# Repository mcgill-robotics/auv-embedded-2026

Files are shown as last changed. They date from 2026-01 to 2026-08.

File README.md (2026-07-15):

# McGill Robotics AUV Embedded 2026

Welcome to the AUV Embedded 2026 repository! This repository is created and maintained by the 2026 McGill Robotics AUV Electrical team. It serves as a platform for sharing, calibrating, and version-controlling the embedded software we develop for our Autonomous Underwater Vehicle (AUV).

## About Us

We are a dedicated team of students from McGill Robotics, focused on designing and implementing the PCBs and embedded systems that power our underwater robot. Our mission is to enable autonomous navigation and task performance through advanced electrical engineering and software development.

## What You'll Find Here

- **Embedded Software**: Source code and libraries for our AUV's embedded systems.
- **Team Structure**: Information about our team members and roles.
- **Tutorials**: Guides and tutorials on using ROS (Robot Operating System) and Arduino for our projects.

For more detail please visit our [Wiki](https://github.com/mcgill-robotics/auv-embedded-2026/wiki).

## Hydrophone related work 

You will find in the `dev/hydrophone` branch the following folders : 
- `documentation`, documenting the design of the new hydrophone ADC board. The documentation was written using _mkdocs_, and to view it you'll need to 1. clone the repository locally, then install mkdocs using `pip install mkdocs` and finally render the web documentation using `mkdocs serve` _in the `documentation` folder_
- `kicad`, which contains the source files (`ADC.kicad_pro`) for the design of the new ADC board
- `ltspice`, for the LTSPICE simulations of the ADC board signal chain.

If you have any questions regarding the hydrophone board design please contact @Oscar-T24

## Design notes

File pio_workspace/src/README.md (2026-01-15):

# Source Code Overview

This directory contains the embedded source code for the McGill Robotics AUV systems. The code is responsible for interfacing with onboard hardware, running micro ROS nodes, and publishing sensor data to the ROS 2 network.

---

## Display Board

The Display Board firmware is implemented in `display_main.cpp`. In addition to handling the TFT display and touchscreen, this board interfaces with a pressure sensor and publishes depth data over micro ROS.

---

## ROS 2 Topics

The following ROS 2 topics are published by the Display Board (`display_main.cpp`).

### Depth Sensor Publisher
- **Node:** `display_node`
- **Source File:** `display_main.cpp`
- **Topic:** `/sensors/depth/z`
- **Message Type:** `std_msgs/msg/Float64`
- **Units:** meters
- **Sensor:** MS5837 (30BA)

The depth value is read from the MS5837 pressure sensor and published periodically using a micro ROS timer.

---

## Publishing Rate (Hz)

The publishing frequency of the depth sensor is controlled by the micro ROS timer defined in `display_main.cpp`:

```cpp
// COPIED PATTERN FROM POWER BOARD
const unsigned int timer_timeout = 1000; // timer period in milliseconds
```

This value represents the **timer period in milliseconds**, not the frequency directly.

### Frequency Formula

```text
timer_timeout_ms = 1000 / frequency_in_hz
```

### Examples

```text
1 Hz  → timer_timeout = 1000
10 Hz → timer_timeout = 100
15 Hz → timer_timeout = 67
20 Hz → timer_timeout = 50
```

For example, to publish depth data at approximately **15 Hz**, use:

```cpp
const unsigned int timer_timeout = 67; // ~15 Hz
```

Because the timer period must be an integer number of milliseconds, some frequencies are approximated.

---

## Notes
- The microROS executor must run at least as fast as the timer period to ensure callbacks are serviced on time.
- Increasing the publish rate increases CPU load and I2C traffic; ensure the sensor and microcontroller can support the selected frequency.

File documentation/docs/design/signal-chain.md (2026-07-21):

## Design of the Signal Chain 

The main components that make up the signal chain are : 

* The analog frontend, which consists of the hydrophone and the preamplifier (ADC driver ADA4950, a FDA)
* The DSP, which consists of the main ADC (AD4001) which sends the digitalized signal over SPI to the MCU
* The voltage reference block, which provides the ADC reference voltage as well as the FDA common mode voltage. 

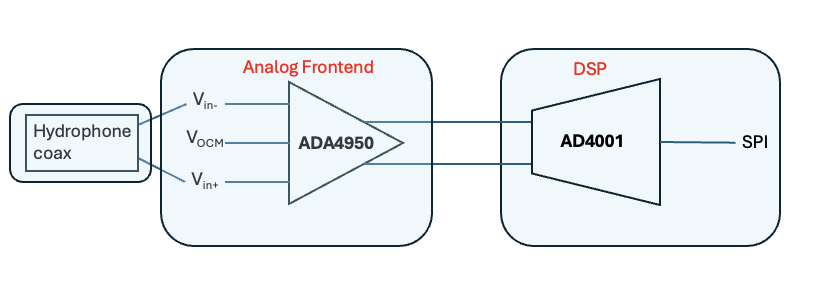
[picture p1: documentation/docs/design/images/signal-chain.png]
High level schematic of the signal chain


### Analog Frontend 

Current considerations to take into account for later and current iterations : 

* Make sure that the input and output voltage range swing is supported by the FDA, given its operating on a single supply
* Maybe add a provisional passive RC filter before the FDA to prevent aliasing of high frequency noise, and that cannot be undone digitally afterwards. Note that the RC filter between the FDA and ADC (aka the "kickback filter") serves a different purpose and does not substitute an anti-aliasing filtger.

### DSP

### List of components with their footprint 

| IC | function | package type | KiCAD library |
|---|---|---| ---|
| ADP7118ARDZ-1.8 | 1.8V LDO | 8-SOIC-EP | [ultra-librarian](https://vendor.ultralibrarian.com/adi/embedded?vdrPN=ADP7118ARDZ-1.8) | 
| ADP7118ARDZ-3.3 | 3.3V LDO | 8-SOIC-EP | [ultra-librarian](https://vendor.ultralibrarian.com/adi/embedded?vdrPN=ADP7118ARDZ-3.3) |
| LTC3265EFE#PBF | charge pump (+/-8.5V) | 20-TSSOP	 | [ultra-librarian](https://vendor.ultralibrarian.com/adi/embedded?vdrPN=LTC3265EFE%23PBF) |
|LTC6373SDFM#PBF | PGA In-amp | 12-DFM | [ultra-librarian](https://vendor.ultralibrarian.com/adi/embedded?vdrPN=LTC6373SDFM%23PBF) | 
| LTC6655BHMS8-1.25#PBF| Precision 1.25V voltage reference | 8-MSOP | [ultra-librarian](https://vendor.ultralibrarian.com/adi/embedded?vdrPN=LTC6655BHMS8-1.25%23PBF) | 
|LTC6655BHMS8-2.5#PBF | Precision 2.5V voltage reference  | 8-MSOP | [ultra-librarian](https://vendor.ultralibrarian.com/adi/embedded?vdrPN=LTC6655BHMS8-2.5%23PBF) | 

The signal chain simulation, which was done on Analog Device's Signal Chain Designer Tool can be accessed at [this link](https://tools.analog.com/en/signalchaindesigner/#session=TKsXolXUHUuK8_GA5aznZQ&step=dEYoxybDQ0WmEA2G54wq2g)

If somehow the link is broken, you can still access the raw data and configuration by downloading [this zip file](./files/Signal%20Chain%20Designer%20data.zip)

Some resources : https://www.analog.com/en/resources/analog-dialogue/articles/next-generation-sar-adc-addresses-precison-data-acquisition.html

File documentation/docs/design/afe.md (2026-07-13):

## Analog frontend

* Programmable Gain Amplifier which amplifies the truly-bipolar signal from the hydrophone and shifts the output-common-mode-voltage ( \(V_{OCM}\) ) to 1.25V
    * LTC6373

### LTC6373

* the effective input resistance between In+ and In- is about \(5 \times 10^{12} \Omega\). The impedance of the pickup coil is in comparison very small. How should we address 

!!! note "Question about input impedance at first stage PGA"
    Should we do smt about the fact that the pickup coil has a very low impedance while the PGA has an _very_ high input impedance ?

* Tow weak pull-down resistors are included before the LTC6373 to ensure the input common mode voltage stays around 0V (`R12`,`R13`)
    * Make sure that this does not introduce input source impedance imbalance as this can very quickly degrade CMRR

The datasheet explicitely mentions that _"A DC path must be provided for the input bias currents of both inputs when a purely differential signal is being amplified"_ so maybe we should keep two resistors then

!!! note "Must consider input current return bias"
    Is that already taken into account with the weak pull-down resistors ? 

According to the datasheet, *the output voltage range depends on whether the LTC6373 differential output is sourcing (\(i_L <0\)) or sinking  (\(i_L > 0\)) current*. Make sure that is sorted out by looking at the input bias of the *ADC driver block*.

!!! alert "To consider"
    More loading from filtering stage (ADC driver block) means reduced output voltage swing at LTC6373 output ! (See figure 61 _"Output voltage swing vs load current and load resistance"_ on Datasheet)

- RFI rectification : High frequency noise couples into coax cable -> generates a DC offset inside the LTC6673
> To cope with this phenomenom it might be necessary to add a LPF (1st order passive RC network is enough) to remove this HF noise

- I chose the `#PBF` option. All four available packages use the DFN footprint, they just differ in temperature range)

Datasheet says input bias current is 25pA max => does that imply anything about the suitable series resistance to put b/w twinax output and LTC6373 input ? 

!!! alert "Checklist to ensure"
    The output common mode voltage (\(V_{OCM}\)) for the LT6373 (=1.25V) is within \(V_{-}+1.5\) and  \(V_{+}-1.5\)

A requirement for the LTC6373 is that the difference between \(V_{+}\) and (\(V_{-}\) (let \(V_s=V_{+}-V_{-}\) _is at least 9V_.

The LTC6373 only accepts an input common mode voltage within -3V to +3V for a +/- 5V power input (for other input voltages Vs see the "Diamond plot")

### MISC

Great resources : [Fully-Differential Amplifiers, Application Report, Texas Instruments 2016](https://www.ti.com/lit/an/sloa054e/sloa054e.pdf)

Another great resource : ["AN 2555 : True bipolar input fully differential output ADC driver design"](https://www.analog.com/media/en/technical-documentation/app-notes/an-2555.pdf)

Another great resource from AD : [AN-1026](https://www.analog.com/media/en/technical-documentation/app-notes/an-1026.pdf)

Another great resource (add the pdf link here) : "Generating Negative voltages from a positive voltage supply (Technical article from AD)"

Great resource from TI : "Fully Differential Op Amps Made Easy"(Application Note,2002)

Great resource from AD : "Generating Negative Voltages from a Positive Voltage Supply: Market Requirements and Solutions"

According to that application report, a FDA generates a "virtual short" between the differential inputs, provided that the a(f) >> 1. But for the LTC6373 the input impedance is much greater (see [power section](/power)). Also compare that "Figure 76. Simplified Block Diagram" in the LTC6373 datasheet.
55 \( \ohms \) then there is extra internal impedance in A1 and A2. 

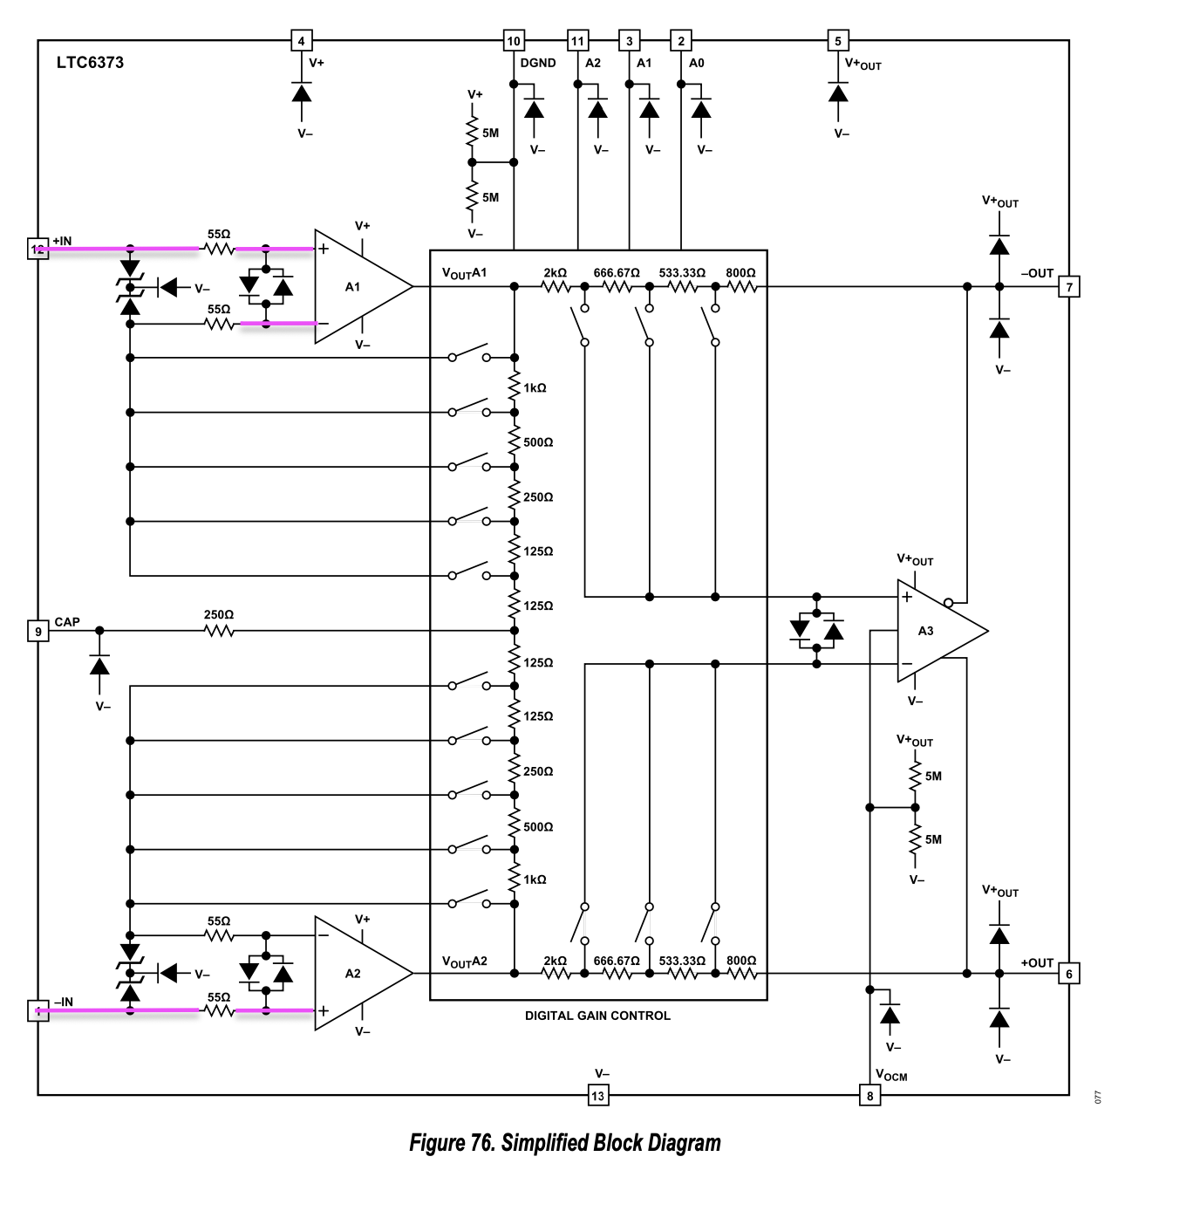
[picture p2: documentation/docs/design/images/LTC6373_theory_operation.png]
Theory of operation of the LTC6373


There seems to be only 55 Ohms series resistors at the input stage (IN-/IN+) but then how does that translate to a M-ohms. 

- Q : should we place a LPF at the very first stage (i.e between twinax and PGA) ? in order to minimize HFI ? What cutoff frequency would we choose such that it is sufficiently \(above 2*f_{max}\)

Simulation on  LTSpice yielded very positive results : 

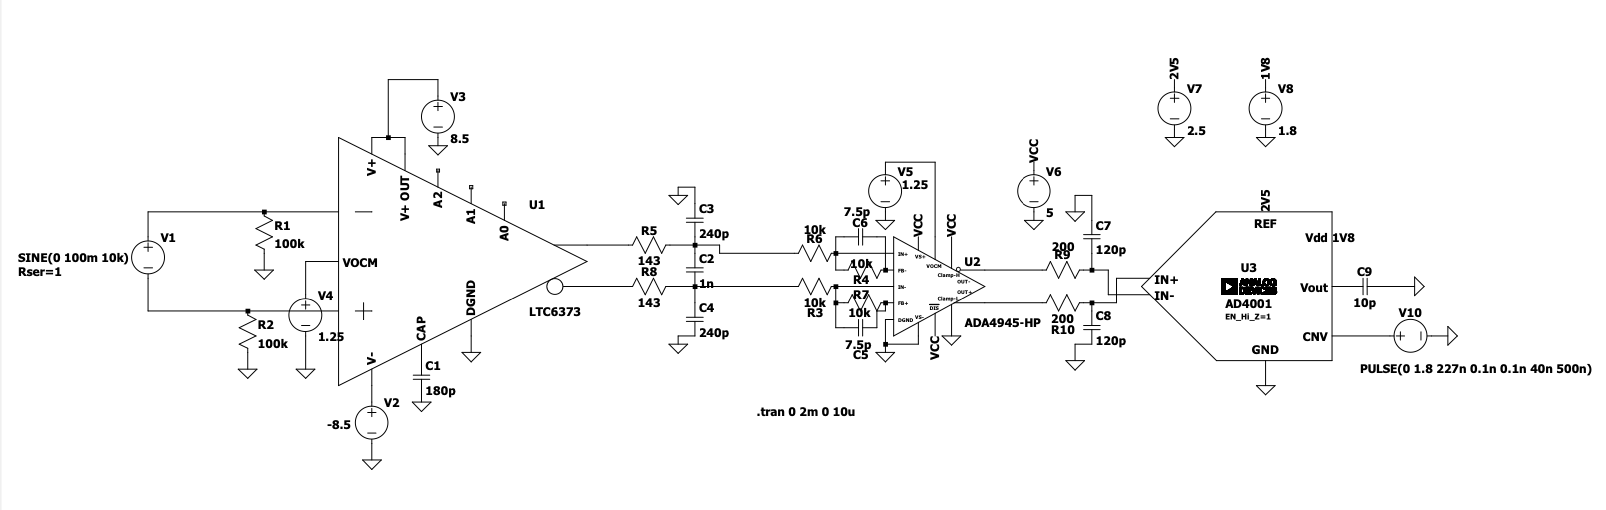
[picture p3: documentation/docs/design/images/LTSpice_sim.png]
Simulation on LTspice


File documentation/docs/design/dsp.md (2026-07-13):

### ADA4945 ADC Driver stage

### AD4001 ADC stage

- A kickback filter (`R5`,`R8`,`C2`,`C12`) was included between the ADA4945 and the AD4001 to help minimize disturbances reflected into the ADC driver from sampling transients (acquire / sample transitions)

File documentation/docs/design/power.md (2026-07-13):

## Power components in the PCB design 

The power components are made up by :

* the standalone LDOs which regulate power for the digital power supplies
    * ADP7118-3.3
    * ADP7118-1.8
* the precision references which are used to set common mode voltages and as the main ADC reference voltage
    * LTC6655B-2.5
    * LTC6655B-1.25
* The dual-supply with boost and inverting charge pump to power the LTC6373 (PGA) with symetric positive and negative supply rails
    * LTC3265

## The LTC3265 (dual supply)

- I chose the TSSOP package instead of the DFN package to make it easier for soldering
- TODO : carefully place and route the LTC3265 in such a way that : 
  1. the fast-switching nets (\(C_{BST+},C_{BST-},C_{INV+},C_{INV-}\)) do not inject noise into analog signal nodes like `ADJ+` and `ADJ-`
  2. the power disspiation is maximized (placing the IC on a corner?) so that thermal heat doesn't build up around the IC
- Choose X5R or X7R ceramic capacitors, they are less sensitive to temperature increases
- The LTC3265 features one _Boost charge pump (which doubles the input voltage)_ coupled to a post-boost LDO, and an _inverting_ charge pump (which generates \(V_{out-}=-V_{IN_N}\)). By connecting \(V_{out+}\) and \(V_{IN_N}\) together we are generating symetric output rails. 
- the `RT` is connected to GND so that the charge pumps work at the maximal constant switching frequency (about 500kHz)
Typical dropout voltages for LDO output pins are given in the table
- According to the datasheet _In constant frequency mode (MODE=0) the values of C_out+ and C_out- directly control the amoubnt of output ripple for a given load current_. The output ripple peak-to-peak voltage being proportional to the load current and inversely proportional to the output capacitance, we cchoose a 100uF capacitance for C_out- and C_out+. The startup time (`t_on`) will be larger but that is not a problem for us. 

Dropout voltage for positive and negative LDOs

| \(V_{dropout_{LDO+}}\) | \(V_{dropout_{LDO-}}\) |
|---|---|
| 400 to 800 mV | 200 to 500mV |

Therefore with a 5V input, we cannot directly generate a stable -5V rail on `LDO-` unless we configure the LTC3265 in symetric mode. 
In that case the maximum post-LDO voltages are about +/- 9V. This gives a very comfortable headroom for the PGA chip.

- Q : what is quiescent current ??

## The LTC6655 (voltage references)

- Dropout voltage is about 500mV, maybe we could connect the first LDO in "chain" with the second one (5V -> 2.5V -> 1.25V instead of 5V -> 1.25V and 5V - >2.5V)
- We chose the 8-lead MSOP package for the simpler soldering. 
- There is a `-NR` (for Noise reduction) package which features a `NR` which we can connect to 0.1uF capacitor for improved noise reduction. 

!!! note "Question about \(V_{LDO+}\) and \(V_{LDO-}\)"
Although the voltage rails can go as high as +/- 9V, is there a sweet spot between power disspated from shifting down \(V_{OUT-/+}\) to \(V_{LDO-/+}\ (the power disspated by the LDO is proportional to these voltage drops) and reasonable headroom in LT6373 power rails ? Figure that out

## The ADP7118 (voltage regulators for 3.3V and 1.8V)

- The dropout voltage is typically 200mV, so we might be able to _chain_ the 1.8V and 3.3V LDOs together instead of connecting each independently to the 5V. 
- Chose the 8-lead SOIC option

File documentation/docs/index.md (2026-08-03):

# Welcome to the home page for the Hydrophone shield design documentation.

For full documentation visit [mkdocs.org](https://www.mkdocs.org).

To look into for later 

https://www.analog.com/en/resources/analog-dialogue/articles/front-end-amp-and-rc-filter-design.html

## Notes about KiCad

The KiCAD project can be found under the `kicad` folder. The project is organized in the following way : 

- `ADC.kicad_sch` main schematics file (other `.kicad_sch` are hierarchical subsheets)
- libraries are in the `kicad/libraries` folder. The libraries are organized in the following way : 
  - `kicad/libraries/footprints` contains all the footprints used in the project
  - `kicad/libraries/symbols` contains all the symbols used in the project
  - `kicad/libraries/3dmodels` contains all the 3D models used in the project

If for some reason a component's footprint or symbol is not found, double check the include path in `Preferences -> Configure Paths`

## Recent changes (design updates)

### August 3rd, 2026

We couldn't find a 100nF ceramic capacitor with package 0603 (1608 metric) for `C18` and `C21` which also have a rated voltage > 8.5V (as they are used to decouple output of charge pump inverter). So we opted for a different package (bigger) = 1206

The BOM can be found in [HERE](design/files/ADC%20BOM.csv)

The zipped Gerber/Drill folder for JLCPCB ordering can be found [HERE](design/files/Aug3Exportv2.zip)

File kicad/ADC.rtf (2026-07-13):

(version 1)
# Custom Design Rules (DRC) for KiCAD 8.0 (Stored in '<project>.kicad_dru' file).

# Matching JLCPCB capabilities: https://jlcpcb.com/capabilities/pcb-capabilities

# KiCad documentation: https://docs.kicad.org/master/id/pcbnew/pcbnew_advanced.html#custom_design_rules

# Inspiration

# - https://gist.github.com/darkxst/f713268e5469645425eed40115fb8b49 (with comments)

# - https://gist.github.com/denniskupec/e163d13b0a64c2044bd259f64659485e (with comments)

# TODO new rule: NPTH pads.

# Inner diameter of pad should be 0.4-0.5 mm larger than NPTH drill diameter.

# JLCPCB: "We make NPTH via dry sealing film process, if customer would like a NPTH but around with pad/copper, our engineer will dig out around pad/copper about 0.2mm-0.25mm, otherwise the metal potion will be flowed into the hole and it becomes a PTH. (there will be no copper dig out optimization for single board)."

# TODO: new rule for plated slots: min diameter/width 0.5mm

# JLCPCB: "The minimum plated slot width is 0.5mm, which is drawn with a pad."

# TODO new rule: non-plated slots: min diameter/width 1.0mm

# JLCPCB: "The minimum Non-Plated Slot Width is 1.0mm, please draw the slot outline in the mechanical layer(GML or GKO)""

# --- Drill/Hole Size ---

(rule "JLCPCB: Drill Hole Size"
# Choose between:

# 1-2 Layers

# (constraint hole_size (min 0.3mm) (max 6.3mm))

# 4-6 Layers (more costly)

# (constraint hole_size (min 0.15mm) (max 6.3mm))

# 4-6 Layers (preferred)

(constraint hole_size (min 0.2mm) (max 6.3mm))
)

(rule "JLCPCB: Via Hole Size"
(condition "A.Type == 'Via'")
# Choose between:

# 1-2 Layers

# (constraint hole_size (min 0.3mm))

# 4-6 Layers (more costly)

# (constraint hole_size (min 0.15mm))

# 4-6 Layers (preferred)

(constraint hole_size (min 0.2mm))
)

(rule "JLCPCB: Via Annular Ring"
(condition "A.Type == 'Via'")
# Choose between:

# 1-6 Layers

# (constraint annular_width (min 0.05mm))

# 1-6 Layers (preferred)

(constraint annular_width (min 0.075mm))
)

(rule "JLCPCB: PTH Hole Size"
(condition "A.Type == 'Pad' && A.Pad_Type == 'Through-hole' && A.isPlated()")
(constraint hole_size (min 0.2mm) (max 6.3mm))
)

(rule "JLCPCB: NPTH Hole Size"
(condition "A.Type == 'Pad' && A.Pad_Type == 'NPTH, mechanical' && !A.isPlated()")
(constraint hole_size (min 0.5mm))
)

# TODO: Hole to board edge ≥ 1 mm. Min. board size 10 × 10 mm.

(rule "JLCPCB: Castellated Hole Size"
(layer outer)
(condition "A.Type == 'Pad' && A.Fabrication_Property == 'Castellated pad'")
(constraint hole_size (min 0.6mm))
)

(rule "JLCPCB: PTH Annular Ring"
(condition "A.Type == 'Pad' && A.Pad_Type == 'Through-hole' && A.isPlated()")
(constraint annular_width (min 0.075mm))
)

(rule "JLCPCB: NPTH Annular Ring"
(condition "A.Type == 'Pad' && A.Pad_Type == 'NPTH, mechanical' && !A.isPlated()")
(constraint annular_width (min 0.25mm))
)

# An expensive 4-Wire Kelvin Test is automatically added for holes that are < 0.3mm with a diameter ≤ 0.4mm.

(rule "JLCPCB: Avoid 4-Wire Kelvin Test"
(condition "(A.Type == 'Via' && A.Hole < 0.3mm && A.Diameter <= 0.4mm) || (A.Type == 'Pad' && ((A.Hole_Size_X < 0.3mm && A.Size_X <= 0.4mm) || (A.Hole_Size_Y < 0.3mm && A.Size_Y <= 0.4mm)))")
# 4-6 Layers

(constraint annular_width (min 0.125mm))
)

# --- VIA Support Rules ---

(rule "JLCPCB: Only Throughhole VIAs are supported"
(condition "A.Type == 'Via'")
(constraint assertion "!(A.isBlindBuriedVia() || A.isMicroVia())")
)

# --- Minimum Clearance ---

(rule "JLCPCB: Hole to Hole Clearance (Different Nets)"
(condition "A.Net != B.Net")
(constraint hole_to_hole (min 0.5mm))
)

(rule "JLCPCB: Via Hole to Via Hole Clearance (Same Net)"
(condition "A.Type == 'Via' && B.Type == 'Via' && A.Net == B.Net")
(constraint hole_to_hole (min 0.254mm))
)

(rule "JLCPCB: Pad to Pad Clearance (Pad without Hole, Different Nets)"
(condition "A.Type == 'Pad' && (A.Pad_Type != 'Through-hole' && A.Pad_Type != 'NPTH, mechanical') && B.Type == 'Pad' && (B.Pad_Type != 'Through-hole' && B.Pad_Type != 'NPTH, mechanical') && A.Net != B.Net")
(constraint clearance (min 0.127mm))
)

(rule "JLCPCB: Pad Hole to Pad Hole Clearance (Pad with Hole, Different Nets)"
(condition "A.Type == 'Pad' && (A.Pad_Type == 'Through-hole' || A.Pad_Type == 'NPTH, mechanical') && B.Type == 'Pad' && (B.Pad_Type == 'Through-hole' || B.Pad_Type == 'NPTH, mechanical') && A.Net != B.Net")
(constraint hole_to_hole (min 0.5mm))
)

# NOTE: This is not stated specifically, but is implied by other rules.

(rule "JLCPCB: Via/Pad to Via/Pad Clearance (Different Nets)"
(condition "(A.Type == 'Pad' || A.Type == 'Via') && (B.Type == 'Pad' || B.Type == 'Via') && A.Net != B.Net")
(constraint clearance (min 0.127mm))
)

# NOTE: This is not stated specifically, but is implied by other rules.

(rule "JLCPCB: Via/Pad Hole to Via/Pad Hole Clearance (Same Net)"
(condition "(A.Type == 'Pad' || A.Type == 'Via') && (B.Type == 'Pad' || B.Type == 'Via') && A.Net == B.Net")
(constraint hole_to_hole (min 0.254mm))
)

(rule "JLCPCB: Via to Trace"
(condition "A.Type == 'Via' && B.Type == 'Track'")
(constraint hole_clearance (min 0.254mm))
)

(rule "JLCPCB: PTH to Trace"
(condition "A.Type == 'Pad' && A.Pad_Type == 'Through-hole' && A.isPlated() && B.Type == 'Track'")
(constraint hole_clearance (min 0.33mm))
)

(rule "JLCPCB: NPTH to Trace"
(condition "A.Type == 'Pad' && A.Pad_Type == 'NPTH, mechanical' && !A.isPlated() && B.Type == 'Track'")
(constraint hole_clearance (min 0.254mm))
)

(rule "JLCPCB: Pad to Trace"
(condition "A.Type == 'Pad' && (A.Pad_Type == 'Through-hole' || A.Pad_Type == 'NPTH, mechanical') && B.Type == 'Track' && A.Net != B.Net")
(constraint clearance (min 0.2mm))
)

# --- Minimum Trace Width and Spacing ---

(rule "JLCPCB: Trace Width (Outer Layer)"
(layer outer)
(condition "A.Type == 'Track'")
# Choose between:

# 1-2 Layers (1oz)

# (constraint track_width (min 0.127mm))

# 4-6 Layers (1oz and 0.5oz)

(constraint track_width (min 0.09mm))
# 1-6 Layers (2oz)

# (constraint track_width (min 0.2mm))

)
(rule "JLCPCB: Trace Spacing (Outer Layer)"
(layer outer)
(condition "A.Type == 'Track' && B.Type == 'Track'")
# Choose between:

# 1-2 Layers (1oz)

# (constraint clearance (min 0.127mm))

# 4-6 Layers (1oz and 0.5oz)

(constraint clearance (min 0.09mm))
# 1-6 Layers (2oz)

# (constraint clearance (min 0.2mm))

)

(rule "JLCPCB: Trace Width (Inner Layer)"
(layer inner)
(condition "A.Type == 'Track'")
# Choose between:

# 4-6 Layers (1oz and 0.5oz)

(constraint track_width (min 0.09mm))
# 4-6 Layers (2oz)

# (constraint track_width (min 0.2mm))

)
(rule "JLCPCB: Trace Spacing (Inner Layer)"
(layer inner)
(condition "A.Type == 'Track' && B.Type == 'Track'")
# Choose between:

# 4-6 Layers (1oz and 0.5oz)

(constraint clearance (min 0.09mm))
# 4-6 Layers (2oz)

# (constraint clearance (min 0.2mm))

)

# --- Legend ---

(rule "JLCPCB: Minimum Line Width"
(layer "?.Silkscreen")
(condition "A.Type == 'Text' || A.Type == 'Text Box'")
(constraint text_thickness (min 0.15mm))
)

(rule "JLCPCB: Minimum Text Height"
(layer "?.Silkscreen")
(condition "A.Type == 'Text' || A.Type == 'Text Box'")
(constraint text_height (min 1mm))
)

(rule "JLCPCB: Pad to Silkscreen"
(condition "A.Type == 'Pad' && ((A.existsOnLayer('F.Mask') && B.Layer == 'F.Silkscreen') || (A.existsOnLayer('B.Mask') && B.Layer == 'B.Silkscreen')) ")
(constraint silk_clearance (min 0.15mm))
)

# --- Board Outlines ---

(rule "JLCPCB: Trace to Board Edge"
(condition "A.Type == 'Track'")
# Choose between:

# Routed

(constraint edge_clearance (min 0.3mm))
# V-Cut Panel

# (constraint edge_clearance (min 0.4mm))

)

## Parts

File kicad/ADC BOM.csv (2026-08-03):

Id | Designator | Footprint | Quantity | Designation | Current Stock | McGill robotics extra stock | Digikey reference
1 | C1, C5, C7, C8, C9, C13, C24, C25, C28, C30, C32, C40, C43, C44, C45 | C_0603_1608Metric_Pad1.08x0.95mm_HandSolder | 15 | 10uF | 10x (0603) | 10x (0603)
2 | C2, C12 | C_0603_1608Metric_Pad1.08x0.95mm_HandSolder | 2 | 120pF |  |  | https://www.digikey.ca/en/products/detail/vishay-vitramon/VJ0603Y121KXJPW1BC/8305331
3 | C3, C6 | C_0603_1608Metric_Pad1.08x0.95mm_HandSolder | 2 | 2.2uF |  |  | https://www.digikey.ca/en/products/detail/murata-electronics/GRM188R71A225KE15D/1033256
4 | C10, C11, C34 | C_0603_1608Metric_Pad1.08x0.95mm_HandSolder | 3 | 0.1uF | 10x (0603) | more than 10 (0603)
5 | C14, C15 | C_0603_1608Metric_Pad1.08x0.95mm_HandSolder | 2 | 10pF |  |  | https://www.digikey.ca/en/products/detail/kyocera-avx/0603YC100KAT2A/3080754
6 | C18, C21 | C_0603_1608Metric_Pad1.08x0.95mm_HandSolder | 2 | 100uF |  |  | https://www.digikey.ca/en/products/detail/cal-chip-electronics-inc/GMC31X5R107M10NT/18151070 | NOTE : using 1206 package because 100nF not available in 0603 imperial
7 | C20, C22 | C_0603_1608Metric_Pad1.08x0.95mm_HandSolder | 2 | 100nF |  |  | 100nF = 0.1uF so we have that already
8 | C23, C26, C27, C29 | C_0603_1608Metric_Pad1.08x0.95mm_HandSolder | 4 | 1uF | 10x (0603) | less than 10 (0603)
9 | C31 | C_0603_1608Metric_Pad1.08x0.95mm_HandSolder | 1 | 180pF |  |  | https://www.digikey.ca/en/products/detail/kemet/C0603C181K3RACTU/2200084
10 | C33, C46, C47 | C_0603_1608Metric_Pad1.08x0.95mm_HandSolder | 3 | 100pF | 10x (0603)
11 | C35 | C_0603_1608Metric_Pad1.08x0.95mm_HandSolder | 1 | 1nF |  |  | https://www.digikey.ca/en/products/detail/kemet/C0603C102K4RECAUTO/8640472
12 | C36, C37 | C_0603_1608Metric_Pad1.08x0.95mm_HandSolder | 2 | 240pF |  |  | https://www.digikey.ca/en/products/detail/kemet/C0603C241G5HACTU/7946365
13 | C38, C39 | C_0603_1608Metric_Pad1.08x0.95mm_HandSolder | 2 | 7.5pF |  |  | https://www.digikey.ca/en/products/detail/cal-chip-electronics-inc/GMT10CG7R5B50NT4/26815062
14 | C41, C42 | C_0603_1608Metric_Pad1.08x0.95mm_HandSolder | 2 | 1pF |  |  | https://www.digikey.ca/en/products/detail/kyocera-avx/KGM15ACG1C1R0BT/3080733
15 | J1, J4 | PinHeader_1x03_P2.54mm_Vertical | 2 | Conn_01x03_Pin
16 | J3 | SAMTEC_CJT-T-P-XX-RA-BH1 | 1 | CJT-T-P-XX-RA-BH1
17 | J5 | PinHeader_1x05_P2.54mm_Vertical | 1 | Conn_01x05_Pin
18 | J6, J7 | PinHeader_1x02_P2.54mm_Vertical | 2 | Conn_01x02_Pin
19 | R2, R3, R4, R7, R10, R11 | R_0603_1608Metric_Pad0.98x0.95mm_HandSolder | 6 | 10k | 10x (0603) | a lot (0603)
20 | R5, R8 | R_0603_1608Metric_Pad0.98x0.95mm_HandSolder | 2 | 200 |  | they have 120Ohms (plenty available) 0603 | https://www.digikey.ca/en/products/detail/panasonic-industry/ERA-3AEB201V/1465837
21 | R6, R9 | R_0603_1608Metric_Pad0.98x0.95mm_HandSolder | 2 | 62.5k |  | they have lots of 51k available | https://www.digikey.ca/en/products/detail/yageo/RC0603JR-0762KL/726818
22 | R12, R13 | R_0603_1608Metric_Pad0.98x0.95mm_HandSolder | 2 | 100k |  | 10x (0603)
23 | R14, R15 | R_0603_1608Metric_Pad0.98x0.95mm_HandSolder | 2 | 143
24 | R16, R18 | R_0603_1608Metric_Pad0.98x0.95mm_HandSolder | 2 | 10 | 10x (0603)
25 | TP2, TP3 | TestPoint_Pad_D1.5mm | 2 | TestPoint
26 | U1 | LFCSP16_ADA4945-1ACPZ-R2_ADI | 1 | ADA4945-1ACPZ-RL
27 | U3 | RD-8-1_ADI | 1 | ADP7118ARDZ-3.3
28 | U4 | RD-8-1_ADI | 1 | ADP7118ARDZ-1.8
29 | U5, U9 | MSOP-8_MS_LIT | 2 | LTC6655CHMS8-1.25-PBF
30 | U6 | MSOP-8_MS_LIT | 1 | LTC6655BHMS8-2.5-PBF
31 | U7 | RM_10_ADI-L | 1 | AD4001BRMZ
32 | U8 | FE_20_ADI | 1 | LTC3265EFE-PBF
33 | U10 | 05-08-1791_ADI | 1 | LTC6373SDFM-PBF

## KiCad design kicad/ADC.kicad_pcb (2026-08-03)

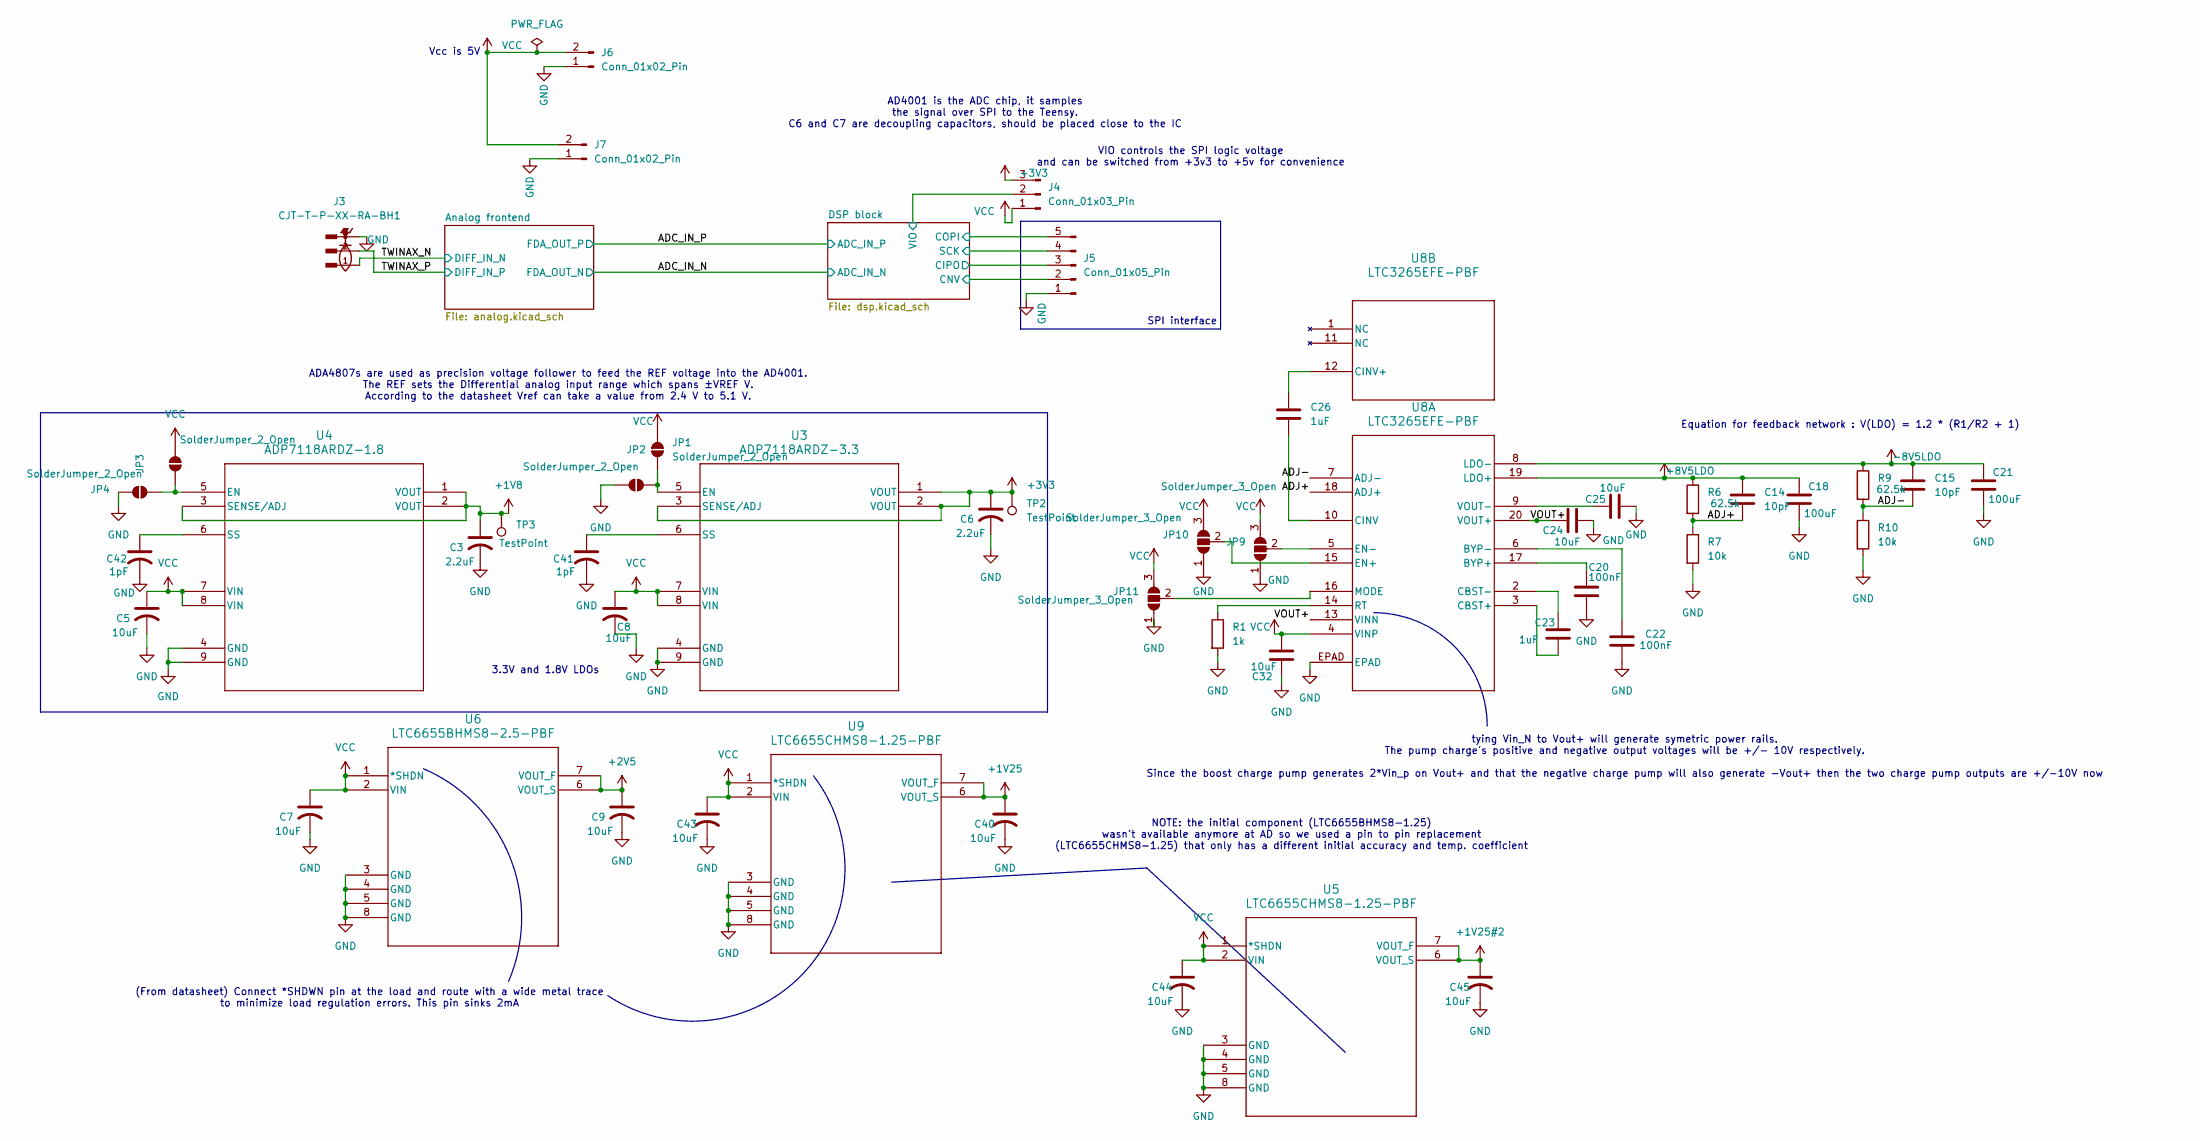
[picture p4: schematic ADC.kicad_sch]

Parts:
C3, C6: 2.2uF; C_0603_1608Metric_Pad1.08x0.95mm_HandSolder
C5, C7, C8, C9, C24, C25, C32, C40, C43, C44, C45: 10uF; C_0603_1608Metric_Pad1.08x0.95mm_HandSolder
C14, C15: 10pF; C_0603_1608Metric_Pad1.08x0.95mm_HandSolder
C18, C21: 100uF; C_1206_3216Metric_Pad1.33x1.80mm_HandSolder
C20, C22: 100nF; C_0603_1608Metric_Pad1.08x0.95mm_HandSolder
C23, C26: 1uF; C_0603_1608Metric_Pad1.08x0.95mm_HandSolder
C41, C42: 1pF; C_0603_1608Metric_Pad1.08x0.95mm_HandSolder
J3: CJT-T-P-XX-RA-BH1; SAMTEC_CJT-T-P-XX-RA-BH1; PARTREV E
J4: Conn_01x03_Pin; PinHeader_1x03_P2.54mm_Vertical
J5: Conn_01x05_Pin; PinHeader_1x05_P2.54mm_Vertical
J6, J7: Conn_01x02_Pin; PinHeader_1x02_P2.54mm_Vertical
JP1, JP2, JP3, JP4: SolderJumper_2_Open; SolderJumper-2_P1.3mm_Open_RoundedPad1.0x1.5mm
JP9, JP10, JP11: SolderJumper_3_Open; SolderJumper-3_P1.3mm_Open_RoundedPad1.0x1.5mm_NumberLabels
R1: 1k
R6, R9: 62.5k; R_0603_1608Metric_Pad0.98x0.95mm_HandSolder
R7, R10: 10k; R_0603_1608Metric_Pad0.98x0.95mm_HandSolder
TP2, TP3: TestPoint; TestPoint_Pad_D1.5mm
U3: ADP7118ARDZ-3.3; RD-8-1_ADI
U4: ADP7118ARDZ-1.8; RD-8-1_ADI
U5, U9: LTC6655CHMS8-1.25-PBF; MSOP-8_MS_LIT
U6: LTC6655BHMS8-2.5-PBF; MSOP-8_MS_LIT
U8: LTC3265EFE-PBF; FE_20_ADI

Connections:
+1V8: C3.1, TP3.1 (1_1), U4.1 (VOUT), U4.2 (VOUT), U4.3 (SENSE/ADJ); also elsewhere on the board
+1V25: C40.1, U9.6 (VOUT_S), U9.7 (VOUT_F); also elsewhere on the board
+1V25#2: C45.1, U5.6 (VOUT_S), U5.7 (VOUT_F); also elsewhere on the board
+2V5: C9.1, U6.6 (VOUT_S), U6.7 (VOUT_F); also elsewhere on the board
+3V3: C6.1, J4.3, TP2.1 (1_1), U3.1 (VOUT), U3.2 (VOUT), U3.3 (SENSE/ADJ)
+8V5LDO: C14.1, C18.1, R6.1, U8.19 (LDO+); also elsewhere on the board
-8V5LDO: C15.1, C21.1, R9.1, U8.8 (LDO-); also elsewhere on the board
/ADJ+: C14.2, R6.2, R7.1, U8.18 (ADJ+)
/ADJ-: C15.2, R9.2, R10.1, U8.7 (ADJ-)
/DSP block/CIPO: J5.3; also elsewhere on the board
/DSP block/CNV: J5.2; also elsewhere on the board
/DSP block/COPI: J5.5; also elsewhere on the board
/DSP block/SCK: J5.4; also elsewhere on the board
/DSP block/VIO: J4.2; also elsewhere on the board
/TWINAX_N: J3.1; also elsewhere on the board
/TWINAX_P: J3.2; also elsewhere on the board
/VOUT+: C24.1, U8.13 (VINN), U8.20 (VOUT+)
GND: C3.2, C5.2, C6.2, C7.2, C8.2, C9.2, C18.2, C20.2, C21.2, C22.2, C24.2, C25.2, C32.1, C40.2, C41.2, C42.2, C43.2, C44.2, C45.2, J3.3, J3.4, J3.5, J3.6, J5.1, J6.1, J7.1, JP2.2 (B), JP4.2 (B), JP9.1 (A), JP10.1 (A), JP11.1 (A), R1.2, R7.2, R10.2, U3.4 (GND), U3.9 (GND), U4.4 (GND), U4.9 (GND), U5.3 (GND), U5.4 (GND), U5.5 (GND), U5.8 (GND), U6.3 (GND), U6.4 (GND), U6.5 (GND), U6.8 (GND), U8.EPAD, U9.3 (GND), U9.4 (GND), U9.5 (GND), U9.8 (GND); also elsewhere on the board
unnamed: JP1.1 (A), JP2.1 (A), U3.5 (EN)
unnamed: JP3.2 (B), JP4.1 (A), U4.5 (EN)
unnamed: JP9.2 (C), U8.5 (EN-)
unnamed: JP10.2 (C), U8.15 (EN+)
unnamed: JP11.2 (C), U8.16 (MODE)
unnamed: C41.1, U3.6 (SS)
unnamed: C42.1, U4.6 (SS)
unnamed: C20.1, U8.17 (BYP+)
unnamed: C22.1, U8.6 (BYP-)
unnamed: C23.2, U8.3 (CBST+)
unnamed: C23.1, U8.2 (CBST-)
unnamed: C26.2, U8.10 (CINV)
unnamed: R1.1, U8.14 (RT)
unnamed: C25.1, U8.9 (VOUT-)
unnamed: C26.1, U8.12 (CINV+)
VCC: C5.1, C7.1, C8.1, C32.2, C43.1, C44.1, J4.1, J6.2, J7.2, JP1.2 (B), JP3.1 (A), JP9.3 (B), JP10.3 (B), JP11.3 (B), U3.7 (VIN), U3.8 (VIN), U4.7 (VIN), U4.8 (VIN), U5.1 (*SHDN), U5.2 (VIN), U6.1 (*SHDN), U6.2 (VIN), U8.4 (VINP), U9.1 (*SHDN), U9.2 (VIN); also elsewhere on the board

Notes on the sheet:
VIO controls the SPI logic voltage and can be switched from +3v3 to +5v for convenience
Vcc is 5V
(From datasheet) Connect *SHDWN pin at the load and route with a wide metal trace to minimize load regulation errors. This pin sinks 2mA
NOTE: the initial component (LTC6655BHMS8-1.25) wasn't available anymore at AD so we used a pin to pin replacement (LTC6655CHMS8-1.25) that only has a different initial accuracy and temp. coefficient
SPI interface
tying Vin_N to Vout+ will generate symetric power rails. The pump charge's positive and negative output voltages will be +/- 10V respectively. Since the boost charge pump generates 2*Vin_p on Vout+ and that the negative charge pump will also generate -Vout+ then the two charge pump outputs are +/-1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
Equation for feedback network : V(LDO) = 1.2 * (R1/R2 + 1)
ADA4807s are used as precision voltage follower to feed the REF voltage into the AD4001. The REF sets the Differential analog input range which spans ±VREF V. According to the datasheet Vref can take a value from 2.4 V to 5.1 V.
3.3V and 1.8V LDOs
AD4001 is the ADC chip, it samples the signal over SPI to the Teensy. C6 and C7 are decoupling capacitors, should be placed close to the IC

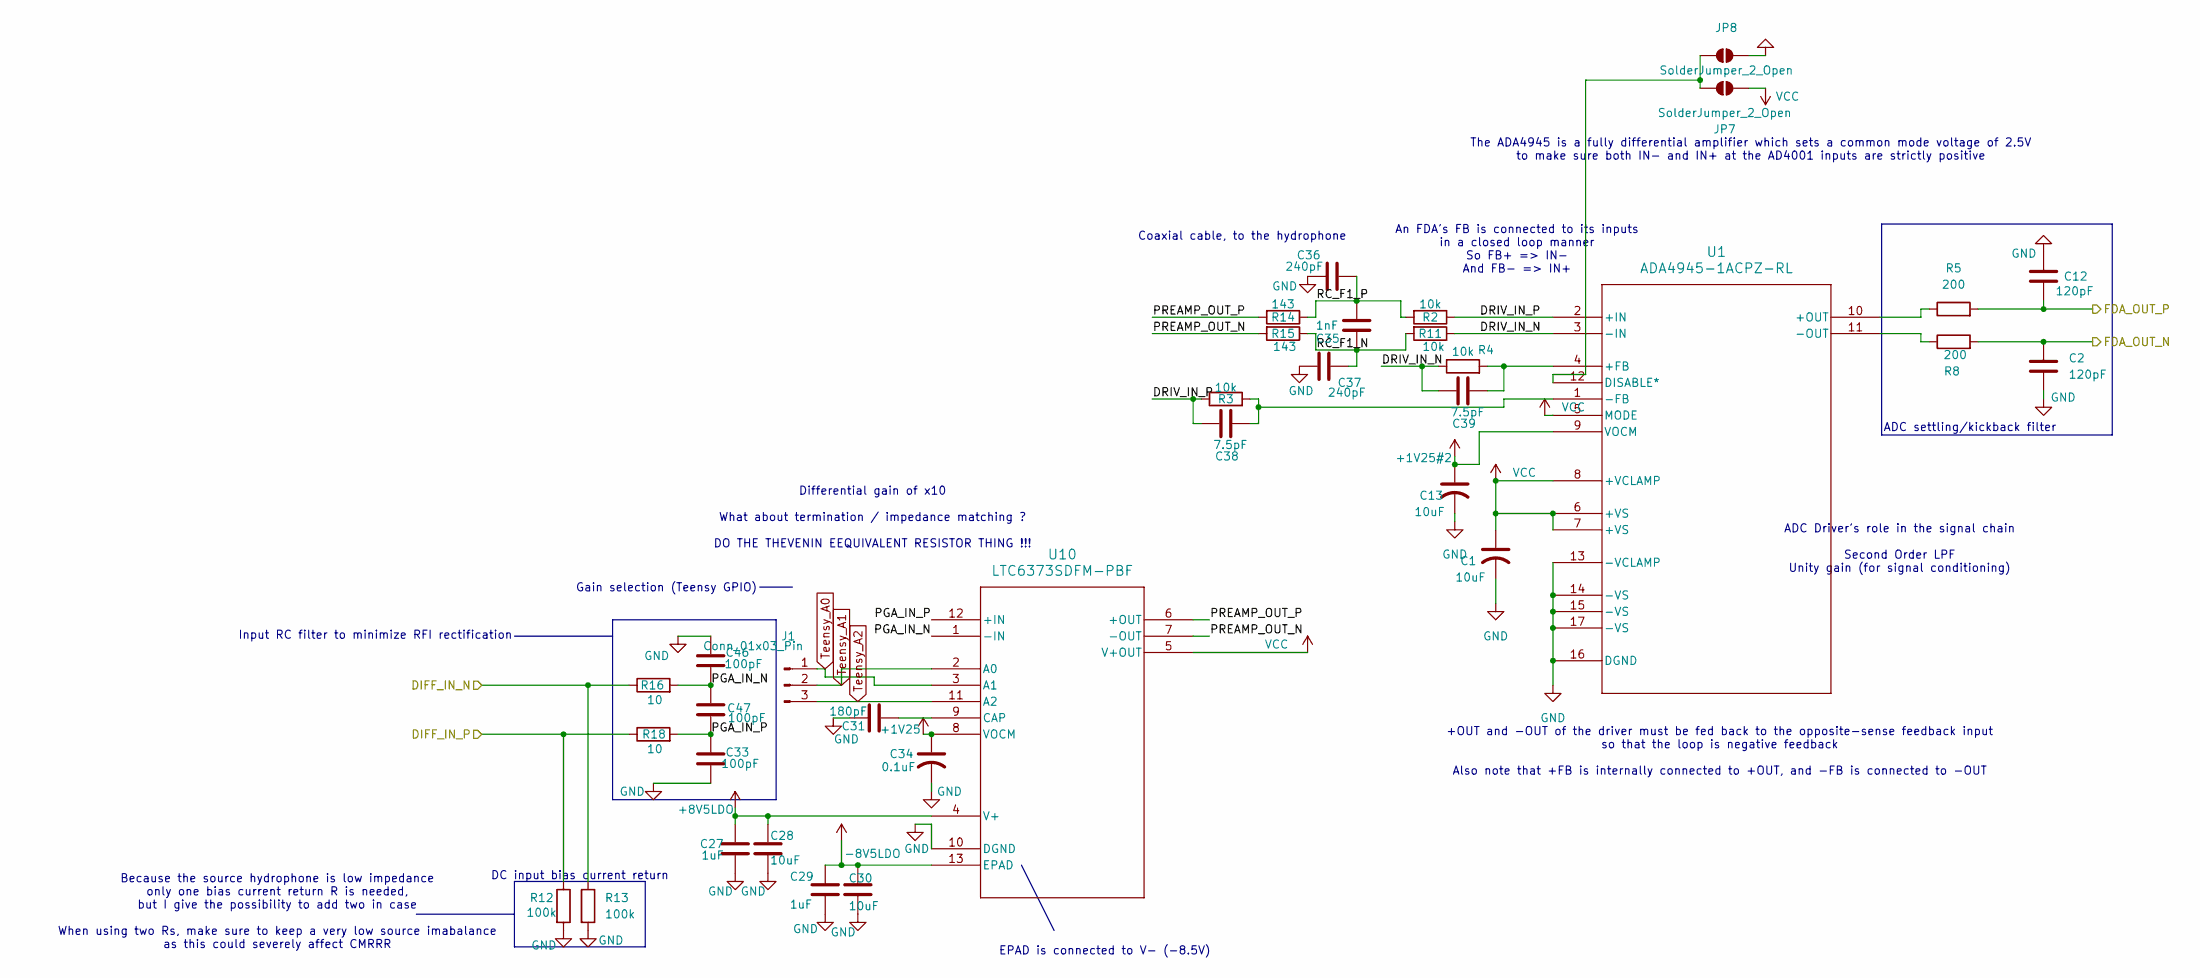
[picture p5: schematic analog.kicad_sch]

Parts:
C1, C13, C28, C30: 10uF; C_0603_1608Metric_Pad1.08x0.95mm_HandSolder
C2, C12: 120pF; C_0603_1608Metric_Pad1.08x0.95mm_HandSolder
C27, C29: 1uF; C_0603_1608Metric_Pad1.08x0.95mm_HandSolder
C31: 180pF; C_0603_1608Metric_Pad1.08x0.95mm_HandSolder
C33, C46, C47: 100pF; C_0603_1608Metric_Pad1.08x0.95mm_HandSolder
C34: 0.1uF; C_0603_1608Metric_Pad1.08x0.95mm_HandSolder
C35: 1nF; C_0603_1608Metric_Pad1.08x0.95mm_HandSolder
C36, C37: 240pF; C_0603_1608Metric_Pad1.08x0.95mm_HandSolder
C38, C39: 7.5pF; C_0603_1608Metric_Pad1.08x0.95mm_HandSolder
J1: Conn_01x03_Pin; PinHeader_1x03_P2.54mm_Vertical
JP7, JP8: SolderJumper_2_Open
R2, R3, R4, R11: 10k; R_0603_1608Metric_Pad0.98x0.95mm_HandSolder
R5, R8: 200; R_0603_1608Metric_Pad0.98x0.95mm_HandSolder
R12, R13: 100k; R_0603_1608Metric_Pad0.98x0.95mm_HandSolder
R14, R15: 143; R_0603_1608Metric_Pad0.98x0.95mm_HandSolder
R16, R18: 10; R_0603_1608Metric_Pad0.98x0.95mm_HandSolder
U1: ADA4945-1ACPZ-RL; LFCSP16_ADA4945-1ACPZ-R2_ADI
U10: LTC6373SDFM-PBF; 05-08-1791_ADI

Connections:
+1V25: C34.1, U10.8 (VOCM); also elsewhere on the board
+1V25#2: C13.1, U1.9 (VOCM); also elsewhere on the board
+8V5LDO: C27.1, C28.1, U10.4 (V+); also elsewhere on the board
-8V5LDO: C29.1, C30.1, U10.13 (EPAD); also elsewhere on the board
/ADC_IN_N: C2.1, R8.2; also elsewhere on the board
/ADC_IN_P: C12.2, R5.2; also elsewhere on the board
/Analog frontend/DRIV_IN_N: C39.2, R4.1, R11.1, U1.3 (-IN)
/Analog frontend/DRIV_IN_P: C38.2, R2.1, R3.1, U1.2 (+IN)
/Analog frontend/PGA_IN_N: C46.1, C47.2, R16.2, U10.1 (-IN)
/Analog frontend/PGA_IN_P: C33.2, C47.1, R18.2, U10.12 (+IN)
/Analog frontend/PREAMP_OUT_N: R15.2, U10.7 (-OUT)
/Analog frontend/PREAMP_OUT_P: R14.2, U10.6 (+OUT)
/Analog frontend/RC_F1_N: C35.1, C37.1, R11.2, R15.1
/Analog frontend/RC_F1_P: C35.2, C36.1, R2.2, R14.1
/TWINAX_N: R13.1, R16.1; also elsewhere on the board
/TWINAX_P: R12.1, R18.1; also elsewhere on the board
GND: C1.2, C2.2, C12.1, C13.2, C27.2, C28.2, C29.2, C30.2, C31.1, C33.1, C34.2, C36.2, C37.2, C46.2, JP8.1 (A), R12.2, R13.2, U1.13 (-VCLAMP), U1.14 (-VS), U1.15 (-VS), U1.16 (DGND), U1.17 (-VS), U10.10 (DGND); also elsewhere on the board
unnamed: JP7.2 (B), JP8.2 (B), U1.12 (DISABLE*)
unnamed: C39.1, R4.2, U1.4 (+FB)
unnamed: R5.1, U1.10 (+OUT)
unnamed: C38.1, R3.2, U1.1 (-FB)
unnamed: R8.1, U1.11 (-OUT)
unnamed: C31.2, U10.9 (CAP)
Teensy_A0: J1.1, U10.3 (A1)
Teensy_A1: J1.2, U10.2 (A0)
Teensy_A2: J1.3, U10.11 (A2)
VCC: C1.1, JP7.1 (A), U1.5 (MODE), U1.6 (+VS), U1.7 (+VS), U1.8 (+VCLAMP), U10.5 (V+OUT); also elsewhere on the board

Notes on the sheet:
ADC Driver's role in the signal chain Second Order LPF Unity gain (for signal conditioning)
An FDA's FB is connected to its inputs in a closed loop manner So FB+ => IN- And FB- => IN+
+OUT and -OUT of the driver must be fed back to the opposite-sense feedback input so that the loop is negative feedback Also note that +FB is internally connected to +OUT, and -FB is connected to -OUT
ADC settling/kickback filter
Gain selection (Teensy GPIO)
DC input bias current return
Differential gain of x10 What about termination / impedance matching ? DO THE THEVENIN EEQUIVALENT RESISTOR THING !!!
Because the source hydrophone is low impedance only one bias current return R is needed, but I give the possibility to add two in case When using two Rs, make sure to keep a very low source imabalance as this could severely affect CMRRR
Coaxial cable, to the hydrophone
EPAD is connected to V- (-8.5V)
Input RC filter to minimize RFI rectification
The ADA4945 is a fully differential amplifier which sets a common mode voltage of 2.5V to make sure both IN- and IN+ at the AD4001 inputs are strictly positive

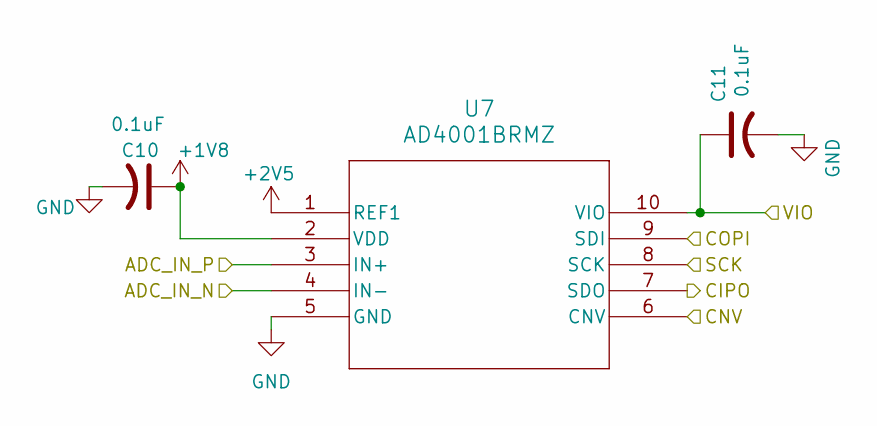
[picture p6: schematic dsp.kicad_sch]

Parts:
C10, C11: 0.1uF; C_0603_1608Metric_Pad1.08x0.95mm_HandSolder
U7: AD4001BRMZ; RM_10_ADI-L

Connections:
+1V8: C10.1, U7.2 (VDD); also elsewhere on the board
+2V5: U7.1 (REF1); also elsewhere on the board
/ADC_IN_N: U7.4 (IN-); also elsewhere on the board
/ADC_IN_P: U7.3 (IN+); also elsewhere on the board
/DSP block/CIPO: U7.7 (SDO); also elsewhere on the board
/DSP block/CNV: U7.6 (CNV); also elsewhere on the board
/DSP block/COPI: U7.9 (SDI); also elsewhere on the board
/DSP block/SCK: U7.8 (SCK); also elsewhere on the board
/DSP block/VIO: C11.1, U7.10 (VIO); also elsewhere on the board
GND: C10.2, C11.2, U7.5 (GND); also elsewhere on the board

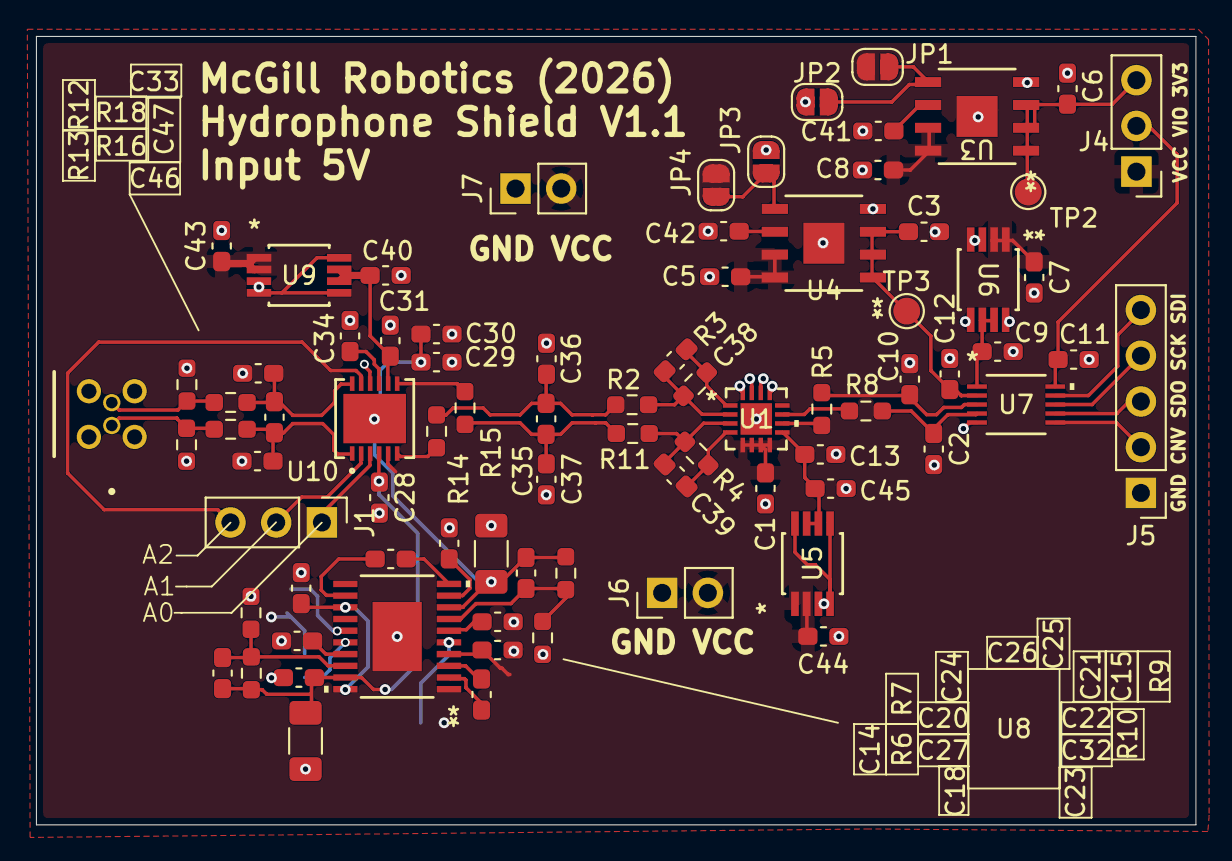
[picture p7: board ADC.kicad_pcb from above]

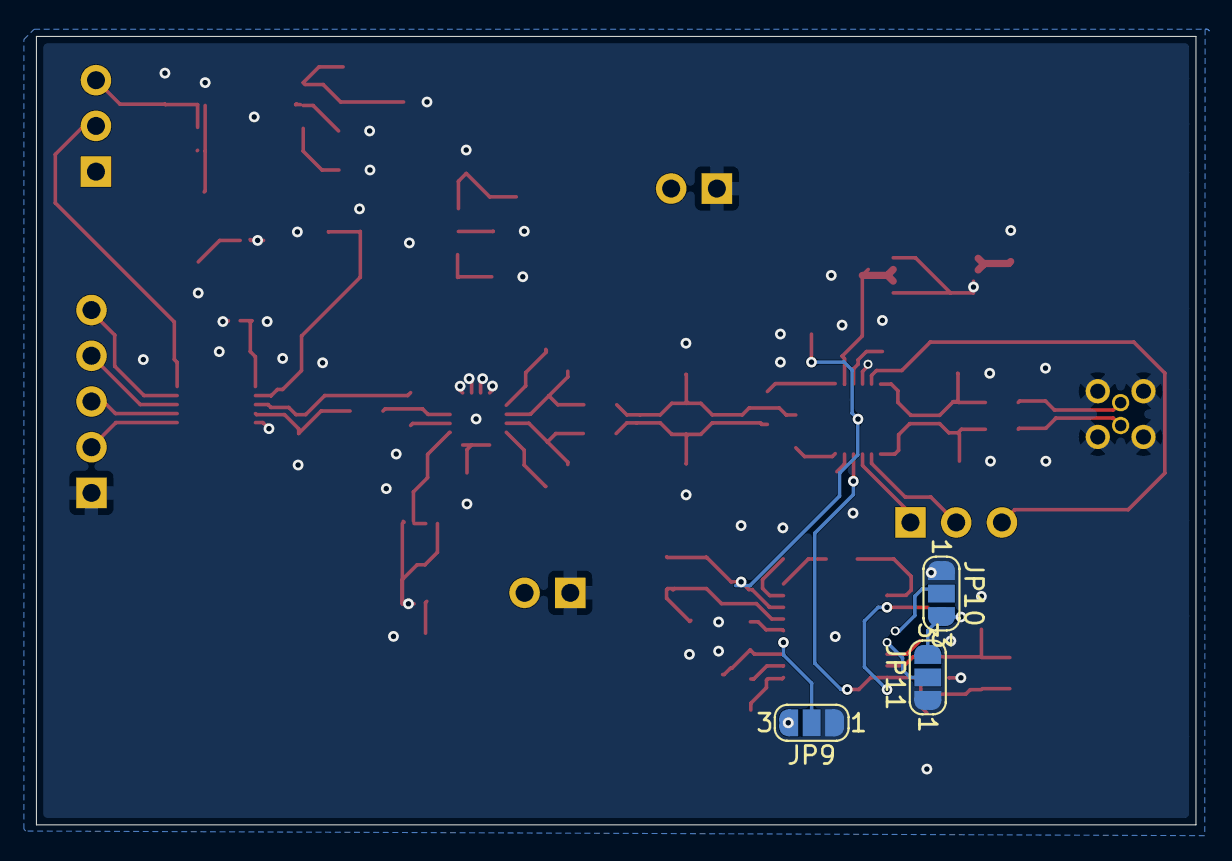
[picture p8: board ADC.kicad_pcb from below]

Board: 2 copper layers, 64.4 x 43.8 mm, 83 parts (3 on the bottom side), 51 nets.

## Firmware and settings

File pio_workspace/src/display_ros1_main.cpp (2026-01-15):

#ifdef DISPLAY_ROS1_H

#include "display_ros1_main.h"

#include "SPI.h"
#include "Adafruit_GFX.h"
#include <iostream>
#include "Adafruit_ILI9341.h"
#include "XPT2046_Touchscreen.h"
#include <SPI.h>       
#include <Adafruit_ILI9341.h>
#include <XPT2046_Touchscreen.h>
#include <Wire.h>
#include "MS5837.h"
#include <ros.h>
#include <auv_msgs/ThrusterMicroseconds.h>
#include <std_msgs/Float32.h>
#include <std_msgs/Float64.h>
#include <std_msgs/Int32.h>
#include <std_msgs/String.h>
#include <cmath>

// Forward declarations (tell the compiler these functions exist)
void initMainPage();
void handleTouch();

// Pin Definitions
#define TFT_DC 9
#define TFT_CS 10
#define TOUCH_CS 8
#define TOUCH_IRQ 2

// Create objects for display and touchscreen
Adafruit_ILI9341 tft = Adafruit_ILI9341(TFT_CS, TFT_DC);
XPT2046_Touchscreen ts(TOUCH_CS);

// Colors
#define BATTERY_COLOR ILI9341_RED
#define NUM_COLOR ILI9341_CYAN
#define LABEL_COLOR ILI9341_RED
#define MAIN_RECT_COLOR ILI9341_WHITE
#define DRY_TEST_COLOR ILI9341_GREEN
#define BACKGROUND_COLOR ILI9341_BLACK

#define BLACK 0x0000
#define BLUE 0x001F
#define RED 0xF800
#define GREEN 0x07E0
#define CYAN 0x07FF
#define MAGENTA 0xF81F
#define YELLOW 0xFFE0
#define WHITE 0xFFFF
#define DARK_GRAY 0x2104
#define LIGHT_GRAY 0xC618

// Display dimensions
#define HEIGHT 240
#define WIDTH 320
#define ILI9341_ROTATION_270 1
#define THRUSTER_SPEED 1540
#define MOVING_AVERAGE_SAMPLES 10

// Initialize sensor object
MS5837 sensor;

// ROS Node Handle
ros::NodeHandle nh;

// ===== Battery/Tether Variables =====
int tether_new = 0;
int tether_old = -1;
int dual_batt_old = -1;
float batt_voltage_1_new = 0.0;
float batt_voltage_2_new = 0.0;
float voltages_old[] = { -1, -1 };
float voltages_new[] = { -1, -1 };
uint16_t batt_colours[] = { WHITE, WHITE };
float voltage_buffer1[MOVING_AVERAGE_SAMPLES];
int voltage_buffer_index1 = 0;
float voltage_buffer2[MOVING_AVERAGE_SAMPLES];
int voltage_buffer_index2 = 0;

String status_new = "Touch 2nd row for surprise";
String status_old = "";

// ===== Thruster/Devices Variables =====
uint16_t microseconds[] = {1500, 1500, 1500, 1500, 1500, 1500, 1500, 1500};
int Sthrusters[8];
int devices_new[] = { 0, 0, 0, 0, 0, 0, 0 };
int thrusters_new[] = { 0, 0, 0, 0, 0, 0, 0, 0 };
float devices_old[] = { -1, -1, -1, -1, -1, -1, -1 };
float thrusters_old[] = { -1, -1, -1, -1, -1, -1, -1, -1 };
bool wasTouched = false;
bool isInDryTestMode = false;
int thruster_states[8] = {0, 0, 0, 0, 0, 0, 0, 0};

// ROS Messages
auv_msgs::ThrusterMicroseconds cmd_msg;
auv_msgs::ThrusterMicroseconds reset_cmd;
std_msgs::Float64 depth_msg;

// Button structure
struct Button {
  int x, y, width, height;
  uint16_t color;
  String label;
};

// Main page buttons
Button buttons[] = {
  {0, 0, 155, 50, BATTERY_COLOR, "0.0V"},
  {160, 0, 155, 50, BATTERY_COLOR, "0.0V"},
  {0, 110, 44, 48, LABEL_COLOR, "IMU"},
  {46, 110, 44, 48, LABEL_COLOR, "P"},
  {92, 110, 44, 48, LABEL_COLOR, "H"},
  {138, 110, 44, 48, LABEL_COLOR, "A"},
  {184, 110, 44, 48, LABEL_COLOR, "FC"},
  {230, 110, 44, 48, LABEL_COLOR, "DC"},
  {276, 110, 44, 48, LABEL_COLOR, "DVL"},
  {0, 164, 320, 30, MAIN_RECT_COLOR, status_new},
  {0, 200, 78, 35, RED, "T"},
  {80, 200, 78, 35, RED, "DB"},
  {160, 200, 78, 35, RED, "Celine"},
  {240, 200, 78, 35, RED, "Mia"},
};

// Thruster buttons for main page
Button buttons_thrusters[] = {
  {0, 55, 38, 50, NUM_COLOR, "1"},
  {40, 55, 38, 50, NUM_COLOR, "2"},
  {80, 55, 38, 50, NUM_COLOR, "3"},
  {120, 55, 38, 50, NUM_COLOR, "4"},
  {160, 55, 38, 50, NUM_COLOR, "5"},
  {200, 55, 38, 50, NUM_COLOR, "6"},
  {240, 55, 38, 50, NUM_COLOR, "7"},
  {280, 55, 38, 50, NUM_COLOR, "8"},
};

// ===== ROS Publishers =====
ros::Publisher DEPTH("/sensors/depth/z", &depth_msg);
ros::Publisher pub("/propulsion/microseconds", &cmd_msg);

// ===== Battery/Tether Functions =====
void tetherStatusMessageCallback(const std_msgs::Int32& msg) {
  tether_new = msg.data;
}

void battery1Callback(const std_msgs::Float32& msg) {
  batt_voltage_1_new = msg.data;
}

void battery2Callback(const std_msgs::Float32& msg) {
  batt_voltage_2_new = msg.data;
}

void publish_depth() {
  depth_msg.data = sensor.depth();
  DEPTH.publish(&depth_msg);
}

void tether_dual_battery(float tether_status, float batt1_V, float batt2_V) {
  uint16_t custom_colors[] = { ILI9341_RED, ILI9341_GREEN };

  int temp_tether_status = tether_status;
  float battery_difference = batt2_V - batt1_V;
  bool temp_battery_status = (battery_difference > -0.05 && battery_difference < 0.05) && (batt1_V >= 12.8 && batt2_V >= 12.8);

  if (temp_tether_status != tether_old) {
    uint16_t tether_color = custom_colors[temp_tether_status];

    tft.fillRoundRect(0, 200, 78, 35, 6, tether_color);
    tft.setTextColor(ILI9341_WHITE);
    tft.setTextSize(2);
    tft.setCursor(33, 210);
    tft.print("T");
    
    tether_old = temp_tether_status;
  }

  if (temp_battery_status != dual_batt_old) {
    uint16_t dual_batt_color = custom_colors[temp_battery_status];

    tft.fillRoundRect(80, 200, 78, 35, 6, dual_batt_color);
    tft.setTextColor(WHITE);
    tft.setTextSize(2);
    tft.setCursor(108, 210);
    tft.print("DB");
    
    dual_batt_old = temp_battery_status;
  }
}

float movingAverage1(float newValue) {
  static float sum = 0;
  sum -= voltage_buffer1[voltage_buffer_index1];
  voltage_buffer1[voltage_buffer_index1] = newValue;
  sum += newValue;
  voltage_buffer_index1 = (voltage_buffer_index1 + 1) % MOVING_AVERAGE_SAMPLES;
  return sum / MOVING_AVERAGE_SAMPLES;
}

float movingAverage2(float newValue) {
  static float sum = 0;
  sum -= voltage_buffer2[voltage_buffer_index2];
  voltage_buffer2[voltage_buffer_index2] = newValue;
  sum += newValue;
  voltage_buffer_index2 = (voltage_buffer_index2 + 1) % MOVING_AVERAGE_SAMPLES;
  return sum / MOVING_AVERAGE_SAMPLES;
}

void batt1(float V1) {
  V1 = round(V1 * 10.0) / 10.0;
  V1 = movingAverage1(V1);
  V1 = round(V1 * 10.0) / 10.0;

  //voltages_new[0] = V1;
  //if (voltages_old[0] != voltages_new[0]) {
    //voltages_old[0] = voltages_new[0];
    // Update display regardless of previous value after page change
    if (voltages_old[0] != V1) {
      voltages_old[0] = V1;

    uint16_t color;
    if (V1 <= 14.8) {
      color = RED;
    } else if (V1 <= 15.8) {
      color = YELLOW;
    } else {
      color = GREEN;
    }

    buttons[0].color = color;
    tft.fillRoundRect(buttons[0].x, buttons[0].y, 
      buttons[0].width, buttons[0].height, 8, color);

    char buffer[6];
    dtostrf(V1, 4, 1, buffer);
    String voltageText = String(buffer) + "V";

    tft.setTextColor(BLACK);
    tft.setTextSize(3);

    int16_t x, y;
    uint16_t w, h;
    tft.getTextBounds(voltageText, 0, 0, &x, &y, &w, &h);
    tft.setCursor(buttons[0].x + (buttons[0].width - w)/2, 
                 buttons[0].y + (buttons[0].height - h)/2);
    tft.print(voltageText);
  }
}

void batt2(float V2) {
  V2 = round(V2 * 10.0) / 10.0;
  V2 = movingAverage2(V2);
  V2 = round(V2 * 10.0) / 10.0;

  voltages_new[1] = V2;
  if (voltages_old[1] != voltages_new[1]) {
    voltages_old[1] = voltages_new[1];

    uint16_t color;
    if (V2 <= 14.8) {
      color = RED;
    } else if (V2 <= 15.8) {
      color = YELLOW;
    } else {
      color = GREEN;
    }

    buttons[1].color = color;
    tft.fillRoundRect(buttons[1].x, buttons[1].y, 
      buttons[1].width, buttons[1].height, 8, color);

    char buffer[6];
    dtostrf(V2, 4, 1, buffer);
    String voltageText = String(buffer) + "V";

    tft.setTextColor(BLACK);
    tft.setTextSize(3);

    int16_t x, y;
    uint16_t w, h;
    tft.getTextBounds(voltageText, 0, 0, &x, &y, &w, &h);
    tft.setCursor(buttons[1].x + (buttons[1].width - w)/2, 
                 buttons[1].y + (buttons[1].height - h)/2);
    tft.print(voltageText);
  }
}

void thrusterStatus(int Sthrusters[]) {
  for (int i = 0; i < 8; i++) {
    if (microseconds[i] == 1500) {
      Sthrusters[i] = 0;
    } else {
      Sthrusters[i] = 1;
    }
  }

}

// == Status Update Functions === //

void updateStatusDisplay(String newStatus) {
  if (newStatus != status_old) {
    tft.fillRoundRect(0, 164, 320, 30, 8, MAIN_RECT_COLOR);

    tft.setTextColor(BLACK);
    tft.setTextSize(2);

    int16_t x, y;
    uint16_t w, h;
    tft.getTextBounds(newStatus, 0,0, &x, &y, &w, &h);
    tft.setCursor((320-w)/2, 164 + (30 - h) / 2);
    tft.print(newStatus);

    status_old = newStatus;
  }
}

// ===== Thruster/Devices Functions =====
void commandCb(const auv_msgs::ThrusterMicroseconds& tc){
  if (isInDryTestMode) {
    return;
  }
  memcpy(microseconds, tc.microseconds, 8*sizeof(uint16_t));
  thrusterStatus(Sthrusters);
}

void devicesIMUMessageCallback(const std_msgs::Int32& msg) {
  devices_new[0] = msg.data;
}

void devicesDVLMessageCallback(const std_msgs::Int32& msg) {
  devices_new[1] = msg.data;
}

void devicesPSMessageCallback(const std_msgs::Int32& msg) {
  devices_new[2] = msg.data;
}

void devicesHYDMessageCallback(const std_msgs::Int32& msg) {
  devices_new[3] = msg.data;
}

void devicesACTMessageCallback(const std_msgs::Int32& msg) {
  devices_new[4] = msg.data;
}

void devicesFCMessageCallback(const std_msgs::Int32& msg) {
  devices_new[5] = msg.data;
}

void devicesDCMessageCallback(const std_msgs::Int32& msg) {
  devices_new[6] = msg.data;
}

void statusMessageCallback(const std_msgs::String& msg) {
  status_new = msg.data;
  updateStatusDisplay(status_new);

}



// ===== ROS Subscribers =====
ros::Subscriber<std_msgs::Int32> sub_tether("/tether/status", &tetherStatusMessageCallback);
ros::Subscriber<std_msgs::Float32> BATT1("/power/batteries/voltage/1", &battery1Callback);
ros::Subscriber<std_msgs::Float32> BATT2("/power/batteries/voltage/2", &battery2Callback);
ros::Subscriber<auv_msgs::ThrusterMicroseconds> sub("/propulsion/microseconds", &commandCb);
ros::Subscriber<std_msgs::Int32> DEVICEIMU("/sensors/imu/status", &devicesIMUMessageCallback);
ros::Subscriber<std_msgs::Int32> DEVICEDVL("/sensors/dvl/status", &devicesDVLMessageCallback);
ros::Subscriber<std_msgs::Int32> DEVICEPS("/sensors/depth/status", &devicesPSMessageCallback);
ros::Subscriber<std_msgs::Int32> DEVICEHYD("/sensors/hydrophones/status", &devicesHYDMessageCallback);
ros::Subscriber<std_msgs::Int32> DEVICEACT("/sensors/actuator/status", &devicesACTMessageCallback);
ros::Subscriber<std_msgs::Int32> DEVICEFC("/sensors/front_camera/status", &devicesFCMessageCallback);
ros::Subscriber<std_msgs::Int32> DEVICEDC("/sensors/down_camera/status", &devicesDCMessageCallback);
ros::Subscriber<std_msgs::String> STATUS_SUB("/mission_display", &statusMessageCallback);

void thrusters(int T1, int T2, int T3, int T4, int T5, int T6, int T7, int T8) {
  if (isInDryTestMode) return;

  int temp_thrusters[] = { T1, T2, T3, T4, T5, T6, T7, T8 };
  uint16_t thruster_colors[] = {WHITE, CYAN};

  for (int i = 0; i < 8; i++) {
    uint16_t color = thruster_colors[temp_thrusters[i]];
    if (temp_thrusters[i] != thrusters_old[i]) {
      buttons_thrusters[i].color = color;
    }
  }

  for (const Button &btn : buttons_thrusters) {
    tft.fillRoundRect(btn.x, btn.y, btn.width, btn.height, 8, btn.color);
    tft.setTextColor(ILI9341_BLACK);
    tft.setCursor(btn.x + 5, btn.y + 10);
    tft.setTextSize(2);
    tft.print(btn.label);
  }

  for (int i = 0; i < 8; i++) {
    thrusters_old[i] = temp_thrusters[i];
  }
}


void device(int IMU, int DVL, int PS, int HYD, int ACT, int FC, int DC) {
  int temp_devices[] = {IMU, DVL, PS, HYD, ACT, FC, DC};
  uint16_t device_colors[] = {RED, GREEN};
  int device_x[] = {0, 276, 46, 92, 138, 184, 230};
  int device_y = 110;
  int device_width = 44;
  int device_height = 48;

  for (int i = 0; i < 7; i++) {
    if (temp_devices[i] != devices_old[i]) {
      uint16_t color = device_colors[temp_devices[i]];
      tft.fillRoundRect(device_x[i], device_y, device_width, device_height, 8, color);

      //tft.setCursor(device_x[i] + 12, device_y + 15);
      tft.setTextColor(WHITE);
      tft.setTextSize(2);
      switch (i) {
        case 0: {
          tft.setCursor(device_x[i] + 4, device_y + 15);
          tft.print("IMU");
          break;
        }
        case 1: {
          tft.setCursor(device_x[i] + 6, device_y + 15);
          tft.print("DVL");
          break;
        }
        case 2: {
          tft.setCursor(device_x[i] + 17, device_y + 15);
          tft.print("P");
          break;
        }
        case 3: {
          tft.setCursor(device_x[i] + 17, device_y + 15);
          tft.print("H");
          break;
        }
        case 4: {
          tft.setCursor(device_x[i] + 17, device_y + 15);
          tft.print("A");
          break;
        }
        case 5: {
          tft.setCursor(device_x[i] + 12, device_y + 15);
          tft.print("FC");
          break;
        }
        case 6: {
          tft.setCursor(device_x[i] + 12, device_y + 15);
          tft.print("DC");
          break;
        }
      }
      devices_old[i] = temp_devices[i];
    }
  }
}

// ===== Dry Test Functions =====
void initializeThrusterMessages() {
  for (int i = 0; i < 8; i++) {
    cmd_msg.microseconds[i] = 1500;
    reset_cmd.microseconds[i] = 1500;
  }
}

void optimized_dry_test(int t) {
  for (int i = 0; i < 8; i++) {
    if (i == t) {
      cmd_msg.microseconds[i] = THRUSTER_SPEED;
    } else {
      cmd_msg.microseconds[i] = 1500;
    }
  }

  if (nh.connected()) {
    pub.publish(&cmd_msg);
    delay(1000);
    pub.publish(&reset_cmd);
  } 
}

void updateThrusters_page2() {
  uint16_t thruster_colors[] = {DARK_GRAY, CYAN};

  for (int i = 0; i < 8; i++) {
    int row = i / 4;
    int col = i % 4;
    int x = 43 + col * 60;
    int y = 65 + row * 60;
    uint16_t color = thruster_colors[thruster_states[i]];

    tft.fillRoundRect(x + 2, y + 2, 46, 46, 10, color);

    tft.setCursor(x + 15, y + 12);
    tft.setTextColor(DARK_GRAY);
    tft.setTextSize(2);
    tft.print(i + 1);
  }
}

void initDryTestPage() {
  tft.setRotation(1);
  tft.fillScreen(BACKGROUND_COLOR);
  
  for (int i = 0; i < 8; i++) {
    int row = i / 4;
    int col = i % 4;
    int x = 43 + col * 60;
    int y = 65 + row * 60;
    tft.drawRoundRect(x, y, 50, 50, 10, LIGHT_GRAY);
  }

  tft.setCursor(WIDTH / 2 - 110, HEIGHT / 3 - 30);
  tft.setTextColor(LIGHT_GRAY);
  tft.setTextSize(1);
  tft.println("-------------Dry Test Mode-------------");

  int backButtonX = 8;
  int backButtonY = 10;
  int backButtonWidth = 60;
  int backButtonHeight = 30;
  tft.fillRoundRect(backButtonX, backButtonY, backButtonWidth, backButtonHeight, 5, LIGHT_GRAY);
  tft.drawRoundRect(backButtonX, backButtonY, backButtonWidth, backButtonHeight, 5, WHITE);
  tft.setCursor(backButtonX + 10, backButtonY + 8);
  tft.setTextColor(DARK_GRAY);
  tft.setTextSize(2);
  tft.print("BACK");
}

// ===== Display Functions =====
void initMainPage() {

  tft.setRotation(1);
  tft.fillScreen(BACKGROUND_COLOR);
  
  for (const Button &btn : buttons) {

    tft.fillRoundRect(btn.x, btn.y, btn.width, btn.height, 8, btn.color);
    if (btn.label == "Touch 2nd row for surprise") {
      tft.setTextColor(BLACK);
    } else {
      tft.setTextColor(WHITE);
    }
    int16_t x, y;
    uint16_t w, h;
    tft.getTextBounds(btn.label, 0, 0, &x, &y, &w, &h);

    if (btn.label != "0.0V") {
      tft.setTextSize(2);
      if (btn.label == "IMU") {
        tft.setCursor(btn.x + (btn.width - w) / 2 - 9, btn.y + (btn.height - h) / 2 - 5);
      } else {
        tft.setCursor(btn.x + (btn.width - w) / 2, btn.y + (btn.height - h) / 2);
      }
      tft.print(btn.label);
    }
  }

  //add this line right after the loop to show the surprise 
  updateStatusDisplay(status_new);

  // Force battery display refresh after page change
  voltages_old[0] = -1;  // Force batt1 to update
  voltages_old[1] = -1;  // Force batt2 to update
  batt1(batt_voltage_1_new);
  batt2(batt_voltage_2_new);
}

void handleTouch() {
  if (ts.touched()) {
    if (!wasTouched) {
      wasTouched = true;
      TS_Point p = ts.getPoint();
      p.x = map(p.x, 300, 4000, 320, 0);
      p.y = map(p.y, 200, 4000, 240, 0);
      int16_t x = p.x;  
      int16_t y = p.y;

      if (!isInDryTestMode) {
        // Main screen button press detection
        if (x >= 0 && x <= 78 && y >= 200 && y <= 235) { // Tether button
          tether_dual_battery(tether_new, batt_voltage_1_new, batt_voltage_2_new);
        }
        else if (x >= 80 && x <= 158 && y >= 200 && y <= 235) { // Dual Battery button
          tether_dual_battery(tether_new, batt_voltage_1_new, batt_voltage_2_new);
        }
        else if (x >= 0 && x <= 300 && y >= 60 && y <= 110) { // Dry Test button
          isInDryTestMode = true;
          initDryTestPage();
        }
      } else {
        // Dry Test Mode button presses
        if (x >= 8 && x <= 68 && y >= 10 && y <= 40) { // BACK button
          isInDryTestMode = false;
          initMainPage();
          batt_voltage_1_new = 0.0;
          batt_voltage_2_new = 0.0;
          batt1(batt_voltage_1_new);
          batt2(batt_voltage_2_new);
          tether_dual_battery(tether_new, batt_voltage_1_new, batt_voltage_2_new);
        } else {
          // Check thruster button presses
          for (int i = 0; i < 8; i++) {
            int row = i / 4;
            int col = i % 4;
            int x_start = 43 + col * 60;
            int y_start = 65 + row * 60;

            if (x >= x_start && x <= x_start + 50 && y >= y_start && y <= y_start + 50) {
              thruster_states[i] = !thruster_states[i];
              updateThrusters_page2();
              optimized_dry_test(i);
              thruster_states[i] = 0;
              updateThrusters_page2();
              break;
            }
          }
        }
      }
    }
  } else {
    wasTouched = false;
  }
}

void display_ros1_setup() {
  // Initialize I2C communication with sensor
  Wire.begin();
  sensor.init();
  delay(1000);

  sensor.setModel(MS5837::MS5837_30BA);
  sensor.setFluidDensity(997);

  tft.begin();
  ts.begin();
  ts.setRotation(1);
  
  nh.initNode();
  nh.subscribe(BATT1);
  nh.subscribe(BATT2);
  nh.subscribe(sub_tether);
  nh.subscribe(sub);
  nh.subscribe(DEVICEIMU);
  nh.subscribe(DEVICEDVL);
  nh.subscribe(DEVICEPS);
  nh.subscribe(DEVICEHYD);
  nh.subscribe(DEVICEACT);
  nh.subscribe(DEVICEFC);
  nh.subscribe(DEVICEDC);
  nh.subscribe(STATUS_SUB);

  nh.advertise(DEPTH);
  nh.advertise(pub);
  initializeThrusterMessages();

  for (int i = 0; i < MOVING_AVERAGE_SAMPLES; i++) {
    voltage_buffer1[i] = 0;
    voltage_buffer2[i] = 0;
  }

  initMainPage();
}

void display_ros1_loop() {
  static unsigned long lastRosUpdate = 0;

  if (millis() - lastRosUpdate > 100) {
    if (!isInDryTestMode) {
      nh.spinOnce();
    }
    lastRosUpdate = millis();
  }

  handleTouch();
  
  // Read sensor data and publish depth
  sensor.read();
  publish_depth();

  // Update display with new data
  batt1(batt_voltage_1_new);
  batt2(batt_voltage_2_new);
  tether_dual_battery(tether_new, batt_voltage_1_new, batt_voltage_2_new);
  device(devices_new[0], devices_new[1], devices_new[2], devices_new[3], 
         devices_new[4], devices_new[5], devices_new[6]);
  thrusters(Sthrusters[0], Sthrusters[1], Sthrusters[2], Sthrusters[3], 
           Sthrusters[4], Sthrusters[5], Sthrusters[6], Sthrusters[7]);

  delay(10);
}

#endif

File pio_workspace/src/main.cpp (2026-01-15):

#include <Arduino.h>

#ifdef ACTUATOR_H
#include "actuator_main.h"
#elif DISPLAY_H
#include "display_main.h"
#elif DISPLAY_ROS1_H
#include "display_ros1_main.h"
#elif DVL_H
#include "dvl_main.h"
#elif POWER_H
#include "power_main.h"
#elif POWER_ROS1_H
#include "power_ros1_main.h"
#elif THRUSTER_TESTS_H
#include "thruster_tests_main.h"
#endif

void setup() {
  #ifdef ACTUATOR_H
    actuator_setup();
  #elif DISPLAY_H
    display_setup();
  #elif DISPLAY_ROS1_H
    display_ros1_setup();
  #elif DVL_H
    dvl_setup();
  #elif POWER_H
    power_setup();
  #elif POWER_ROS1_H
    power_ros1_setup();
  #elif THRUSTER_TESTS_H
    thruster_tests_setup();
  #endif
}

void loop() {
  #ifdef ACTUATOR_H
    actuator_loop();
  #elif DISPLAY_H
    display_loop();
  #elif DISPLAY_ROS1_H
    display_ros1_loop();
  #elif DVL_H
    dvl_loop();
  #elif POWER_H
    power_loop();
  #elif POWER_ROS1_H
    power_ros1_loop();
  #elif THRUSTER_TESTS_H
    thruster_tests_loop();
  #endif
}

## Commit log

2025-10-06 fixed battery voltage text color from white to black, hopefully it works
2025-10-25 optimizing display code to make depth sensor more efficient with depth_sensor_opti.cpp
2025-11-29 First Version of Depth Sensor Code in ROS2
2025-11-29 shifted and moved display ros 2 code with env and, headers, and renamed original code -- to be tested with real display board. builds successfully
2026-01-08 updated code to remove LED pin - it works
2026-01-08 Update README with depth sensor publishing details
    Clarified the description of the depth sensor publishing rate and added examples for timer timeout calculations.
2026-06-23 added KiCad files and refactored Kicad imports to be encapsulated into the project working directory
    [ADC-B_Cu.gbl, ADC-B_Mask.gbs, ADC-B_Paste.gbp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]
